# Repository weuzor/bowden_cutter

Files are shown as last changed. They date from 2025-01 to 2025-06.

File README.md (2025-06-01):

# Bowden Filament Cutter for the Voron Stealthburner

toolhead_CW2
toolhead_G2E
actuator

## Introduction
This toolhead integrated filament cutter cuts filament similar to the [filametrix mod](https://github.com/sorted01/Filametrix), on which it is based on, but uses a different approach for actuation by means of an external high torque servo which is connected to the toolhead via a bowden cable.
This way the cutting process is independent of toolhead position/movement and does not introduce any forces to the printer kinematics.

The modification consists of 4 components: a __modified extruder front body__ with bowden cable routing, a __modified printhead__ with shuttle guiding, the __blade shuttle__ and an __external actuator__ which can be clamped to the printer frame extrusions.

## Underlying designs

Because a filament cutter is only useful for multi material printing and multi material printing is very little fun without ECAS and filament sensors the following desings were used as a base instead of the original CW2 or [G2E](https://github.com/JaredC01/Galileo2) parts:

The modified extruder front body for the CW2 is based on [this design](https://www.printables.com/model/466692-stealthburner-cw2-filament-sensors-with-ecas-latch/files) with ECAS and two 5.5mm steelball/microswitch filament sensors

The modified extruder front body for the G2E is based on [this design](https://github.com/juliusjj25/G2E-Filametrix-Lever-Switch-Mod) with ECAS and two DF2-L3-D3 microswitch filament sensors

The printheads are based on the [original voron design printheads](https://vorondesign.com/voron_stealthburner) and the filametrix mod.

## Recent Changes

The original design worked fine, but when cutting harder filaments the required pulling force caused the blade shuttle to tilt when the spring was fully compressed.
Allthough still working this is not nice to look at and also results in unnecessary forces trying to push the extruder to the left and the printhead to the right.
To fix this a limit stop for the blade shuttle has been added to the extruder parts. This limit stop also acts as a switch which closes when the blade shuttle pulley bearing touches the limit stop.

Before:
https://github.com/user-attachments/assets/2ef3fe31-b55a-4e68-ab35-1ae4be9e5d9d

After:
https://github.com/user-attachments/assets/6c915074-667b-457e-bb91-5009137e85ce

After some time of use, the wire puller part of the actuator gets sliced in half by the thin wire.
Printing that part 100% infill helps, but to fix this issue for good the new part has two additional reinforcement screws. Also, some knurling has been added for more comfortable turning by hand.

---
# Modification Steps
## __Blade Shuttle__
### Required hardware
* 1 [ID 3 x OD 10 x 3 mm V-Groove Bearing](https://www.amazon.com/Atoplee-3x10x3mm-603VV-Groove-Bearings/dp/B0191I4UU2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)
* 1 M2.5 x 8 countersunk head screw  -OR-  M2.5 x 8 screw + Brass tube OD 3 mm / ID 2.5 mm, L 3 mm 
* 1 M2.5 washer
* 1 M2.5 x 5 x 3.5 heat set insert ([from this assortment](https://www.amazon.com/Threaded-Inserts-Assortment-Printing-Injection/dp/B0D49Y8J6M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))
* 1 compression spring 5.5 x 17 mm ([from this assortment](https://www.amazon.com/dp/B0DF21GRN1/ref=sr_1_1_sspa?__mk_de_DE=ÅMÅŽÕÑ&crid=2AKV6FXLFZY04&dib=eyJ2IjoiMSJ9.B9q0atkenJRq4xFEpuA6kf0xvpWVwtjE_6Jrg8n_wl6NHta9ITOqniu6mMLtZMFY2_GtR4F_p8Hx75KQDkPY7fpfaDna87tC5B3B3hsjJfN4gQ8lqOv1fjgLgXU953trXPpknKVWs0QRSiNBvWAiD5JjdxLaEr9TSl6Sqnwv4ecXGIxPsb15RojaRq2vxIcHnsdGiSbCrEg-Z74QEsWqzqf3JAr6EFOmu-LbFnp-Fyk.SwDMcXsodjg3r6qEAGHaBXy8vgAhajbzSszQWizHb5c&dib_tag=se&keywords=compression+spring&qid=1736647255&sprefix=compression+spring%2Caps%2C199&sr=8-1-spons&sp_csd=d2lkZ2V0TmFtZT1zcF9hdGY&psc=1))
* 1 [Hobby knife blade # 4](https://www.amazon.com/CIMAXIC-Manganese-Carving-Replacement-Supplies/dp/B0DJX43D77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) (cut or broken off at the end of the slot)
### Printed parts
| Picture | Description | STL | STEP |
| :---: | :---: | :---: | :---: |
| Shuttle | Blade shuttle  | [stl](https://github.com/weuzor/bowden_cutter/blob/main/STL/Blade%20Shuttle%20Parts/Shuttle.stl) | [step](https://github.com/weuzor/bowden_cutter/blob/main/CAD/Blade%20Shuttle%20Parts/Shuttle.step) |
### Assembly
* Break off the blade #4 near the end of the slot
* Install the heat set insert in the printed part 
* Assemble as shown.
  Note: Unfortunately the blade slot width is too small for a M3 screw to fit through, so M2.5 it has to be. However, the pulley inner diameter is 3 mm. In order to keep the pulley centered either use something like a brass tube OD 3 mm / ID 2.5 mm, L 3 mm or some heatshrink over the last 3 mm of the screw thread.
Altertnatively, a well tightened countersunk head screw can also be used.
Blade Shuttle Assembly Option 1
Blade Shuttle Assembly Option 2
blade_shuttle_and_spring

---
## Extruder 
### Required hardware
* PTFE Tube 1mm/2mm (inner tube) ([amazon](https://www.amazon.com/Quickun-Teflon-Tubing-Printer-Length/dp/B08Q83XNTT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))
* PTFE tube 2mm/4mm (outer tube) ([amazon](https://www.amazon.com/Quickun-Teflon-Tubing-Printer-Length/dp/B08Q813BQV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))
Note: The inner tube must fit into the outer tube. There are some tubes sold as 2mm inner diameter where this is possible and some where it is not.
If you cannot find appropriate outer tubing use one with 2.5 mm inner diameter instead.
* Nylon coated stranded steel wire 0.6 mm diameter ([amazon](https://www.amazon.com/BENECREAT-120-Feet-0-024inch-7-Strand-Stainless/dp/B07V3S947N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))
* 2 M1.6 x 3 Screws
* Appropriate wires and connectors for the toolhead board ([amazon](https://www.amazon.com/-/de/dp/B07S18D3RN/ref=sr_1_3?__mk_de_DE=ÅMÅŽÕÑ&crid=1RZAB60IVHYBH&dib=eyJ2IjoiMSJ9.JP_2nZAq6AIUN2Ys6pJIe-n5ac8OQy-y538Uq2oHmvDcXHvzcv4dG5FbggURIH8csrpxDbXchWkjJbL9Wnd__2dbPNm_JHhf7BwQRyl2se9LbzNYUa_mLgD2P_9uNHQ7wXC8hG95_oQttkY4tPxC2TDGVdnoDqUKz8O7TaGJxfN9JhqeRNCXgB3kL8-n2MlSkEJE6QzaYFYSTF0LyOS10SIeVXFIrw0yxfg5jZr6r8uPnggjhcjj2l3E-idA0MmEyoQc7XXNf0CMzDxTZ6QSrQz_a64CsHYt5yr4c1mwS6UVCC2pxMZv3POeD3AnGr-b_yHVYOl2kf7ldo9kumGNRLfi1l4th5g8wTo4Ldu6GA9U9YJdbALKhyqKVnMNHmcDDiQyaBrm9ThWswQUmxQod8EJ7Fdf6C8AlHTYVTGA11oSLuOa4UzsCe9qVAeEU7IB.hZfWDVEpQwBFOSOiRrlumKK7xhQUQ_z9sIYtyja4n0Q&dib_tag=se&keywords=mx+1.25&qid=1739485194&sprefix=mx+1.25%2Caps%2C197&sr=8-3) for SB2209)
### Printed parts
#### Galileo 2
| Picture | Description | STL | STEP |
| :---: | :---: | :---: | :---: |
| G2E_Front_Body | G2E Front Body with two ball less filament sensors, bowden tube routing, ECAS, cutter endstop | [stl](https://github.com/weuzor/bowden_cutter/blob/main/STL/Extruder%20Parts/G2E/G2E_Front_Body.stl) | [step](https://github.com/weuzor/bowden_cutter/blob/main/CAD/Extruder%20Parts/G2E/G2E_Front_Body.step) | 
#### Clockwork 2
| Picture | Description | STL | STEP |
| :---: | :---: | :---: | :---: |
| CW2 Front Body (new) | CW2 Front Body (new motor plate) with two filament sensors, bowden tube routing, ECAS, cutter endstop | [stl](https://github.com/weuzor/bowden_cutter/blob/main/STL/Extruder%20Parts/CW2/CW2_Front_Body_new_motorplate.stl) | [step](https://github.com/weuzor/bowden_cutter/blob/main/CAD/Extruder%20Parts/CW2/CW2_Front_Body_new_motorplate.step) |
| CW2 Front Body (old) | Same as above but compatible with the old motor plate | [stl](https://github.com/weuzor/bowden_cutter/blob/main/STL/Extruder%20Parts/CW2/CW2_Front_Body_old_motorplate.stl) | [step](https://github.com/weuzor/bowden_cutter/blob/main/CAD/Extruder%20Parts/CW2/CW2_Front_Body_old_motorplate.step) |
### Assembly
* Cut the 2mm/4mm PTFE tube to the required length for the installation (depending on printer size and where the actuator will be located).
* Cut the 1mm/2mm PTFE tube approximately 10 cm longer than the 2mm/4mm tube
* Tie a [figure-8-knot](https://www.animatedknots.com/figure-8-knot) in the 0.6 mm wire and cut it approximately 10 cm longer than the 1mm/2mm PTFE tube (measured from the knot)
* Check that the OD 4 mm PTFE fits into its recess on top of the printed body. Clear out by hand with a 4mm drill if necessary.
* Check that the 0.6 mm wire can be inserted in the small holes at the bottom aof the printed body. Clear out by hand with a 1 mm drill if necessary.
* Push the OD 2 mm PTFE from the top into the printed body until it is fully inserted. Might need a bit of persuasion here and there but is definitely doable. A drop of oil and a 2 steps forward one step back movement strategy helps. If you can insert the 0.6 mm wire from the opposite side without catching the on the PTFE tube edge you are there.
* Slide the ID 2mm OD 4mm PTFE over the ID 1 mm OD 2mm PTFE tube and push firmly into its recess in the printed part.
* Cut the inner PTFE tube flush with the outer tube
* Push the 0.6 mm wire through the long hole at the bottom of the printed part and pull firmly to fully tighten the knot. Clip off the excess wire leaving about 1 mm.
* After a U-turn push the wire through the PTFE until it comes out the other end
* Route the cables along the cable path as shown and insert approx. 2mm of tinned wire into each hole in the limit stop and press downward.
* Screw in the two M1.6 screws into the two holes (above the wires) in the limit stop as shown. Check for continuity with a Multimeter (screw head to end of wire).
* Complete the extruder with the modified body part
bowden_installation_cw2
bowden_installation_g2e
cut_sensor_inst
cut_sensor

---
## Printhead
### Required hardware
* 1 M3 Nut
* Filament path PTFE Tube
### Printed parts
#### E-RV
| Picture | Description | STL | STEP |
| :---: | :---: | :---: | :---: |
| E-RV (no ADXL)_Front E-RV (no ADXL)_Back | E-RV Printhead (symmetric, no ADXL mount) with blade shuttle guiding | [front](https://github.com/weuzor/bowden_cutter/blob/main/STL/Printhead%20Parts/E-RV/E-RV%20(no%20ADXL)_Front.stl) [back](https://github.com/weuzor/bowden_cutter/blob/main/STL/Printhead%20Parts/E-RV/E-RV%20(no%20ADXL)_Back.stl) | [front](https://github.com/weuzor/bowden_cutter/blob/main/CAD/Printhead%20Parts/E-RV/E-RV%20(no%20ADXL)_Front.step) [back](https://github.com/weuzor/bowden_cutter/blob/main/CAD/Printhead%20Parts/E-RV/E-RV%20(no%20ADXL)_Back.step) |
| E-RV_Front E-RV_Back | Stock E-RV printhead with blade shuttle linear guiding  | [front](https://github.com/weuzor/bowden_cutter/blob/main/STL/Printhead%20Parts/E-RV/E-RV_Front.stl) [back](https://github.com/weuzor/bowden_cutter/blob/main/STL/Printhead%20Parts/E-RV/E-RV_Back.stl) | [front](https://github.com/weuzor/bowden_cutter/blob/main/CAD/Printhead%20Parts/E-RV/E-RV_Front.step) [back](https://github.com/weuzor/bowden_cutter/blob/main/CAD/Printhead%20Parts/E-RV/E-RV_Back.step) |
#### P-RPDV2
| Picture | Description | STL | STEP |
| :---: | :---: | :---: | :---: |
| P-RPDV2_Front P-RPDV2_Back | Stock P-RPDV2 printhead with blade shuttle linear guiding  | [front](https://github.com/weuzor/bowden_cutter/blob/main/STL/Printhead%20Parts/P-RPDV2/P-RPDV2_Front.stl) [back](https://github.com/weuzor/bowden_cutter/blob/main/STL/Printhead%20Parts/P-RPDV2/P-RPDV2_Back.stl) | [front](https://github.com/weuzor/bowden_cutter/blob/main/CAD/Printhead%20Parts/P-RPDV2/P-RPDV2_Front.step) [back](https://github.com/weuzor/bowden_cutter/blob/main/CAD/Printhead%20Parts/P-RPDV2/P-RPDV2_Back.step) |
#### P-DRG
| Picture | Description | STL | STEP |
| :---: | :---: | :---: | :---: |
| P-DRG_Front P-DRG_Back | Stock P-DRG printhead with blade shuttle linear guiding  | [front](https://github.com/weuzor/bowden_cutter/blob/main/STL/Printhead%20Parts/P-DRG/P-DRG_Front.stl) [back](https://github.com/weuzor/bowden_cutter/blob/main/STL/Printhead%20Parts/P-DRG/P-DRG_Back.stl) | [front](https://github.com/weuzor/bowden_cutter/blob/main/CAD/Printhead%20Parts/P-DRG/P-DRG_Front.step) [back](https://github.com/weuzor/bowden_cutter/blob/main/CAD/Printhead%20Parts/P-DRG/P-DRG_Back.step) |
### Assembly

*  Assemble as usual. Don't forget the ptfe tube before inserting the M3 nut
*  Check that the spring followed by the blade shuttle can be inserted into the guide and moves smoothly
*  Optionally lubricate the contact surfaces with a tiny amount of petroleum jelly
*  Remove blade shuttle and spring for now

shuttle_insert
shuttle_inserted
shuttle_cut_pos

---

## Actuator

### Required hardware
* 1 [Miuzei 25kg Servo](https://www.amazon.com/Miuzei-Waterproof-Compatible-Steering-Horn（270°）/dp/B0C5LTKBD4/ref=sr_1_8?crid=1RKYBOP2MC3X5&dib=eyJ2IjoiMSJ9.5BsLf39L1mf4c0ZP7ihNfBcTucSXzqrylZ5wPm1FCZv5wywgXEZg8dzhwaeOFhQKoNJWUU3jyFHMdI_3LbyACR33Kmu10v0dFclbm8f5Wi29QDhH9nP2OV--_QzTVKYJtExh0ru4tfxeGZCQR1O45u62ZbZ7vDu3kLlgaTb16AaTpBTvtNuceMTKtBs_AoUUucpRz8daa88bTl0jgQc3zPhm-HagKRoHf3OntGky96HSfhzFnBvgk_47v8lISK_yfMscdNapOXOrRZh-QcGOnMjBkn3Q2Z7BgruQQfZQg2Dosnl2Lo9nXBHNfwN3vcMU5GP0gaHs4a_NLZ4IQaibOTazYqvwFS1RVYBUXIoopTEp9_zGB0G0D4ItZ_uS9RlO99e3KistSzl-Ztef1v2GcOVwoBLVwRXQxPFw_HdreqIyc5iuHV7sSS0DYl1A8Qrn._j4nZ8dHQSZ3S-M3PkTiq-Yw1uM0tN85bQJuZTc3dog&dib_tag=se&keywords=miuzei&qid=1738536290&sprefix=miuzei%2Caps%2C181&sr=8-8&th=1) (or similar) + supplied screws + round servo horn
* 4 M3 x 4 x 5 heat set inserts
* 4 M3 washer
* 2 M3 x 5 screws
* 2 M3 x 12 screws
* 4 M2 x 8 Tapping screws
* 1 ECAS Collet (rubber part removed)
### Printed parts
| Picture | Description | STL | STEP |
| :---: | :---: | :---: | :---: |
| Servo_Frame_Mount | Actuator servo to frame mount | [stl](https://github.com/weuzor/bowden_cutter/blob/main/STL/Actuator%20Parts/Servo_Frame_Mount.stl) | [step](https://github.com/weuzor/bowden_cutter/blob/main/CAD/Actuator%20Parts/Servo_Frame_Mount.step) |
| Servo_Frame_Mount_Mirrored | Actuator servo to frame mount, mirrored | [stl](https://github.com/weuzor/bowden_cutter/blob/main/STL/Actuator%20Parts/Servo_Frame_Mount_mirrored.stl) | [step](https://github.com/weuzor/bowden_cutter/blob/main/CAD/Actuator%20Parts/Servo_Frame_Mount_mirrored.step) |
| Servo_Frame_Mount_Clamp_Insert | clamp insert ( x2 ) | [stl](https://github.com/weuzor/bowden_cutter/blob/main/STL/Actuator%20Parts/Servo_Frame_Mount_Clamp_Insert_x2.stl) | [step](https://github.com/weuzor/bowden_cutter/blob/main/CAD/Actuator%20Parts/Servo_Frame_Mount_Clamp_Insert_x2.step) |
| Wire_Puller | wire puller servo attachment| [stl](https://github.com/weuzor/bowden_cutter/blob/main/STL/Actuator%20Parts/Wire_Puller.stl) | [step](https://github.com/weuzor/bowden_cutter/blob/main/CAD/Actuator%20Parts/Wire_Puller.step) |
| Wire_Puller_V2 | wire puller servo attachment with reinforcement screws | [stl](https://github.com/weuzor/bowden_cutter/blob/main/STL/Actuator%20Parts/Wire_Puller_strong.stl) | [step](https://github.com/weuzor/bowden_cutter/blob/main/CAD/Actuator%20Parts/Wire_Puller_strong.step) |
### Assembly
* Press the ECAS collet and two clamp inserts into the servo mount body as shown
* Install the two heat set inserts in the wire puller part and assemble as shown with the round servo horn which comes with the servo.
* Combine everything as shown
actuator_body
actuator_puller
actuator_servoy

## FINAL STEPS
actuator_wire
shuttle_pos

* Assemble the toolhead with the modified extruder and printhead
* Run the bowden wire through the actuator hole and insert the ptfe tubes into the ecas collet
* Insert the blade shuttle and place the wire loop around the pulley
* Loosen the wire clamp bolts and route the wire on the actuator servo as shown
* Adjust the wire length so that the blade shuttle is flush with the printhead edge and the servo is approximately in the shown position (servo angle 90 deg)
* Tighten the wire clamp bolts

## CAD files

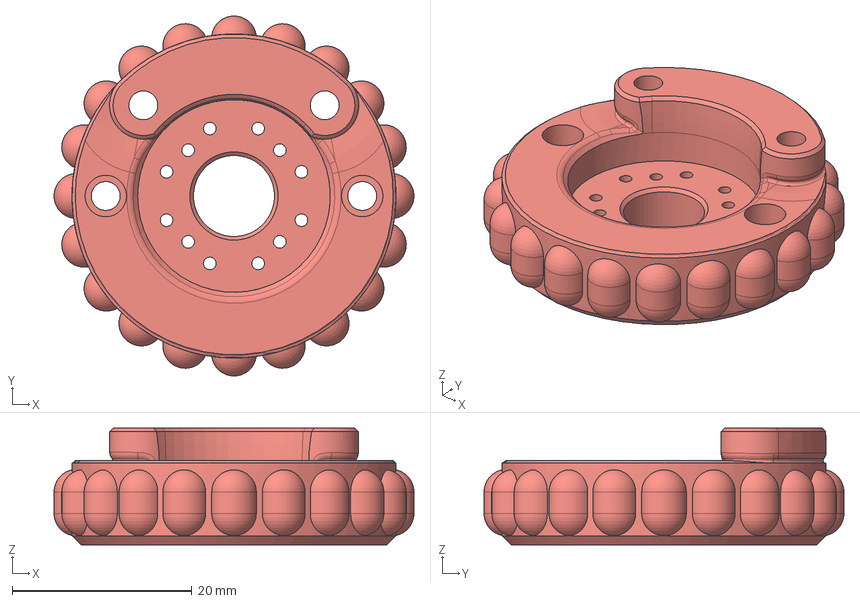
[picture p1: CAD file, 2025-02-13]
CAD/Actuator Parts/Wire_Puller_strong.step
40.0 x 40.0 x 13.0 mm

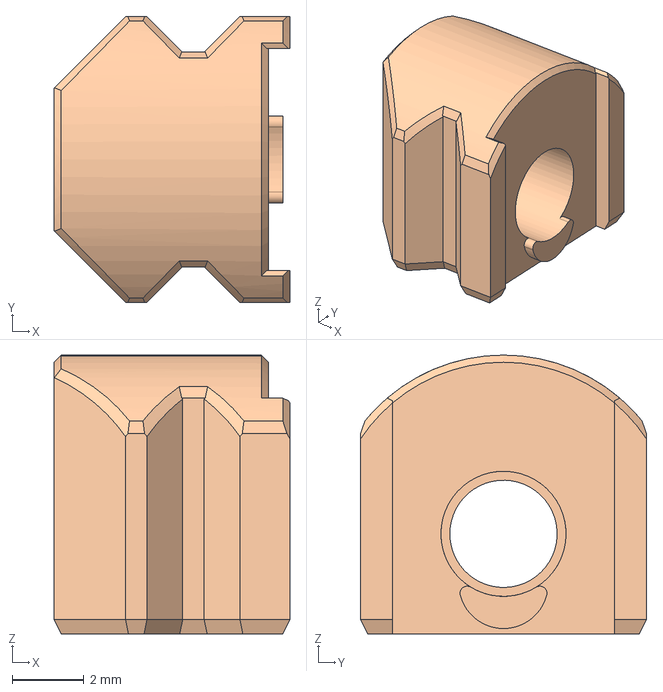
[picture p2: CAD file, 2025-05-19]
CAD/Blade Shuttle Parts/Shuttle v2.step
6.60 x 8.00 x 7.80 mm

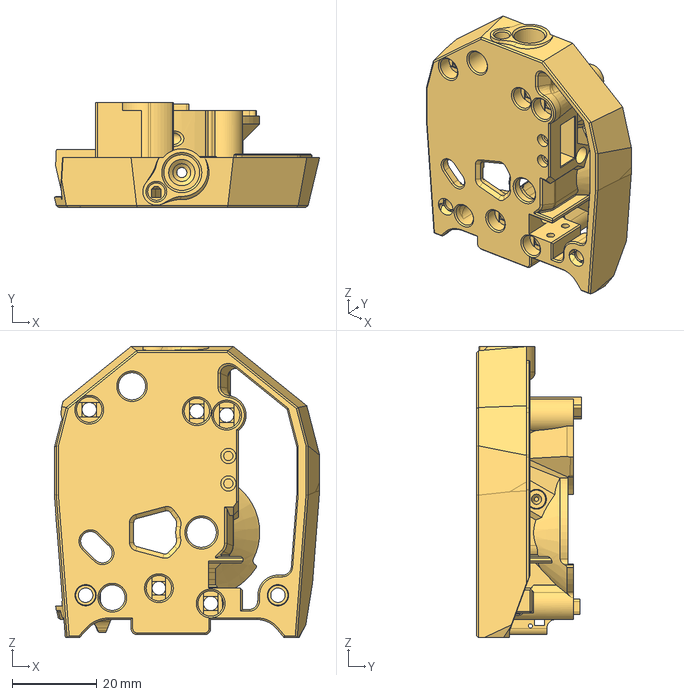
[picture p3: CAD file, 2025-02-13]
CAD/Extruder Parts/CW2/CW2_Front_Body_new_motorplate.step
62.6 x 24.7 x 68.7 mm

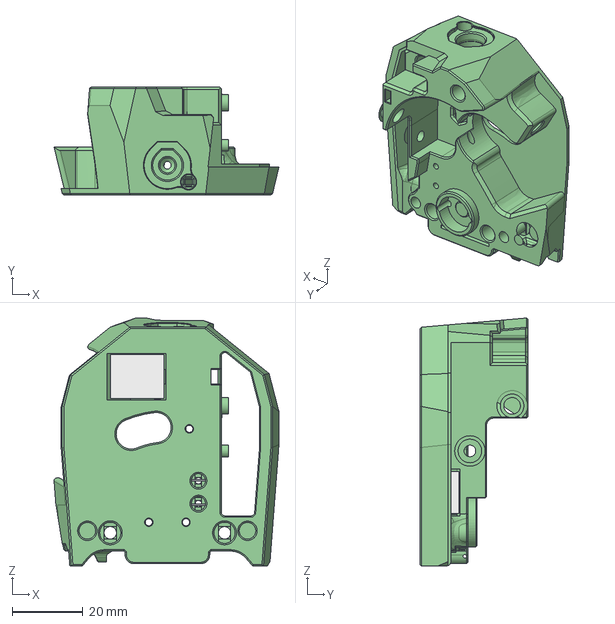
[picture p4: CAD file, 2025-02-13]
CAD/Extruder Parts/G2E/G2E_Front_Body.step
63.8 x 30.6 x 70.3 mm

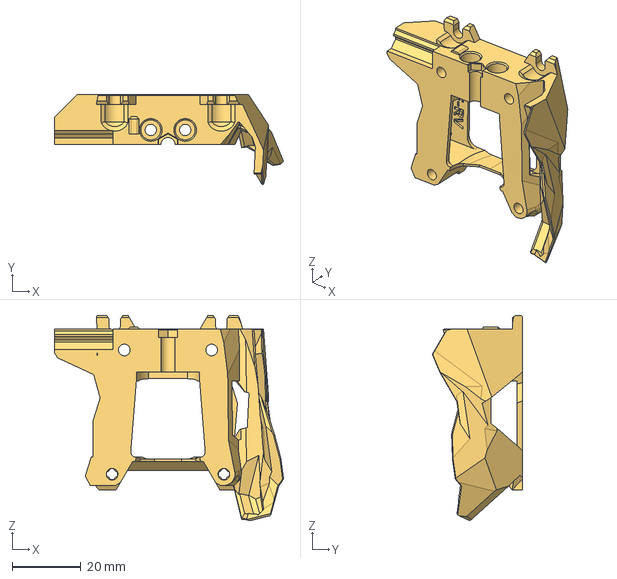
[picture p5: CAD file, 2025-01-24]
CAD/Printhead Parts/E-RV/E-RV_Back.step
66.6 x 26.3 x 59.7 mm

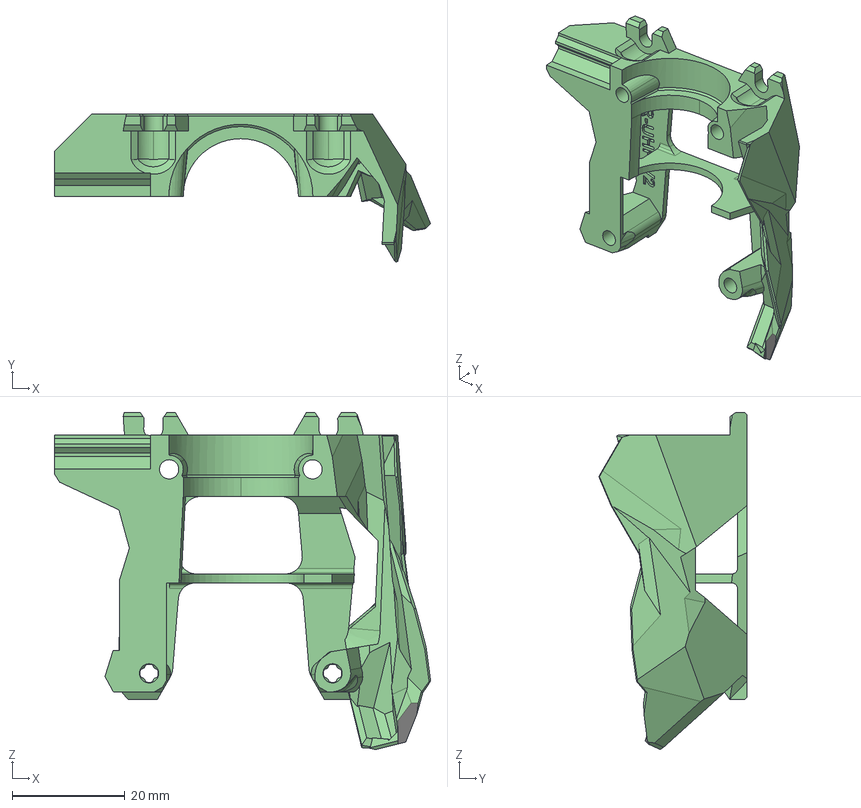
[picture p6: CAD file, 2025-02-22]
CAD/Printhead Parts/P-RPDV2-UHF/P-RPDV2-UHF_Rear.step
66.6 x 26.3 x 59.7 mm

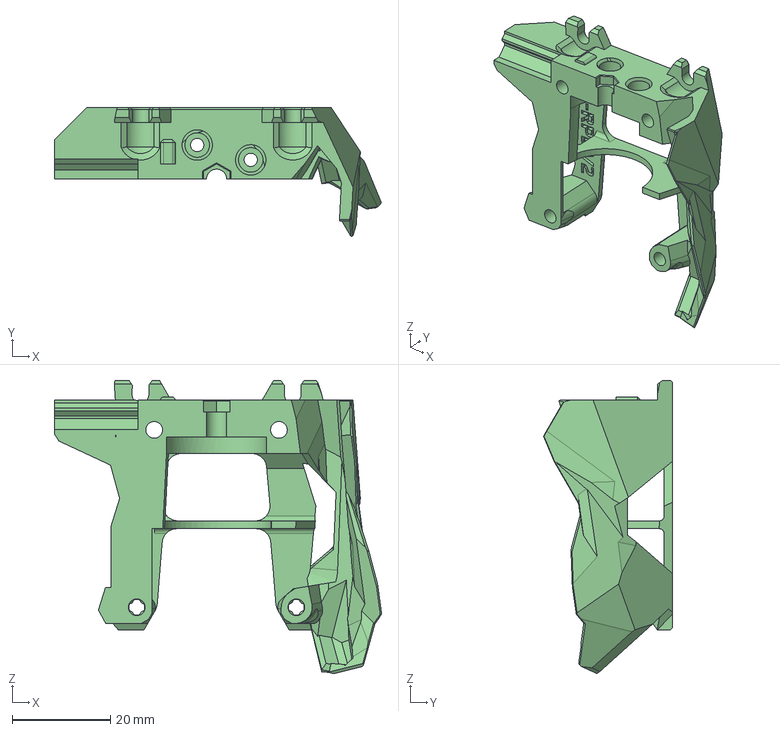
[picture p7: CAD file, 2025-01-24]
CAD/Printhead Parts/P-RPDV2/P-RPDV2_Back.step
66.6 x 26.3 x 59.7 mm

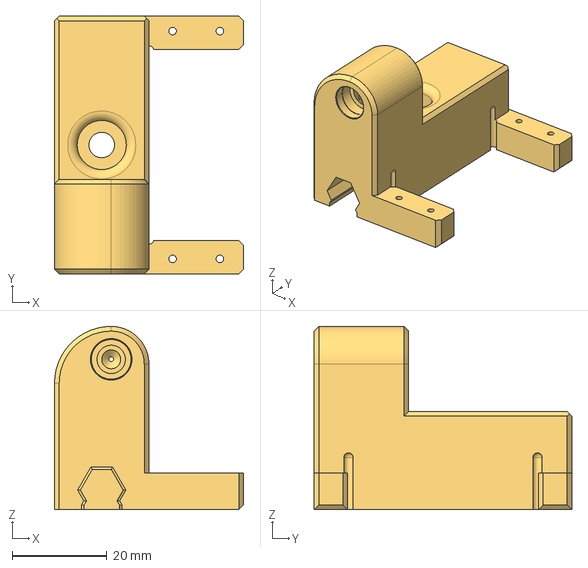
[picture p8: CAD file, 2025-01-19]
CAD/Actuator Parts/Servo_Frame_Mount_mirrored.step
40.0 x 54.5 x 38.8 mm

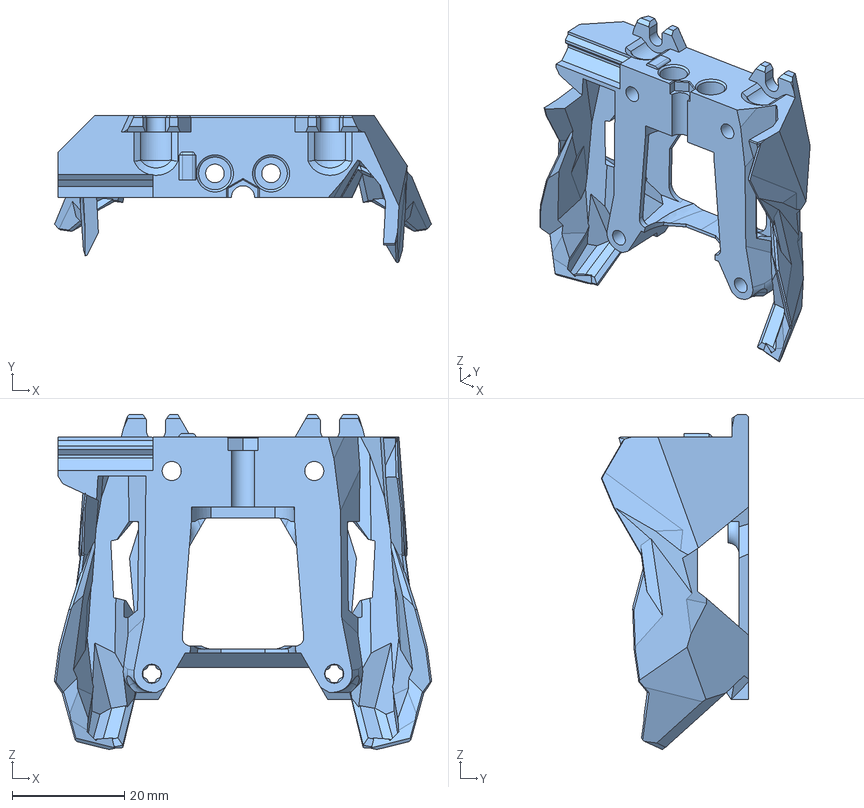
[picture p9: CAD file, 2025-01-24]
CAD/Printhead Parts/E-RV/E-RV (no ADXL)_Back.step
67.2 x 26.3 x 59.7 mm

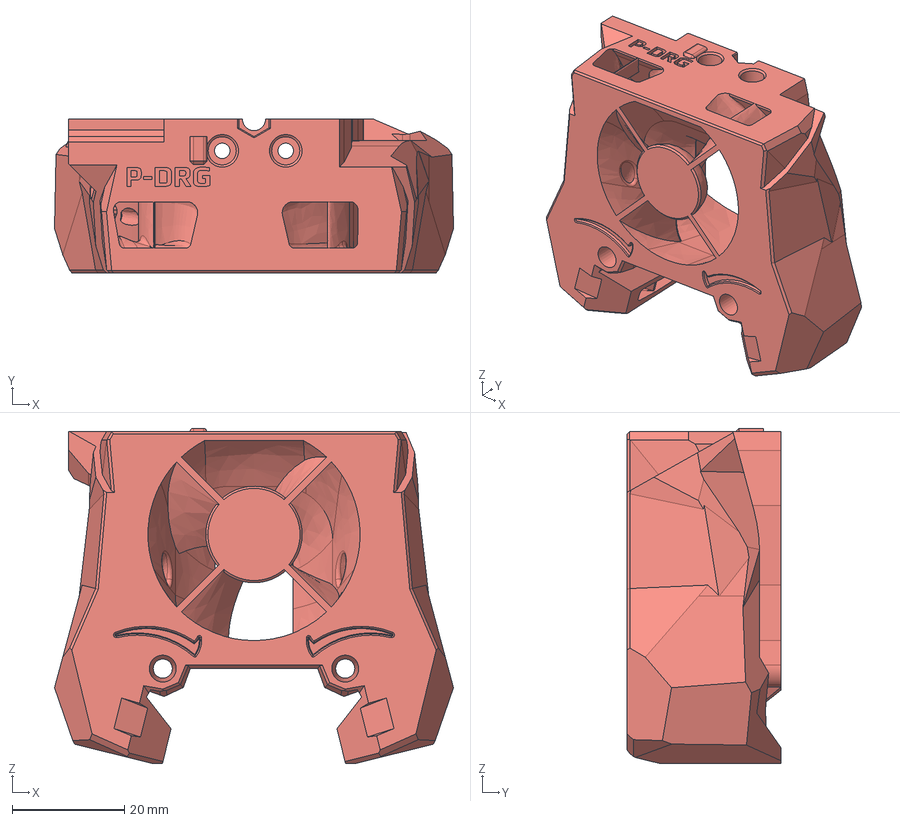
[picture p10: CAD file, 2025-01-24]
CAD/Printhead Parts/P-DRG/P-DRG_Front.step
71.1 x 27.4 x 59.7 mm

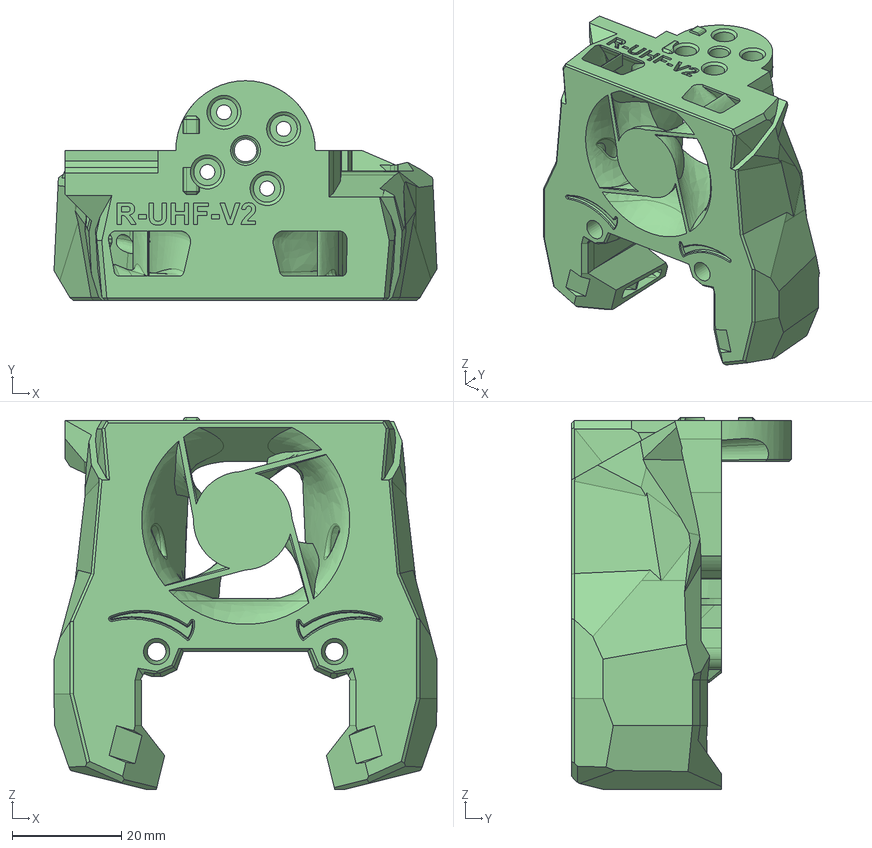
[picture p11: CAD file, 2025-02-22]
CAD/Printhead Parts/P-RPDV2-UHF/P-RPDV2-UHF_Front.step
70.0 x 40.2 x 68.0 mm

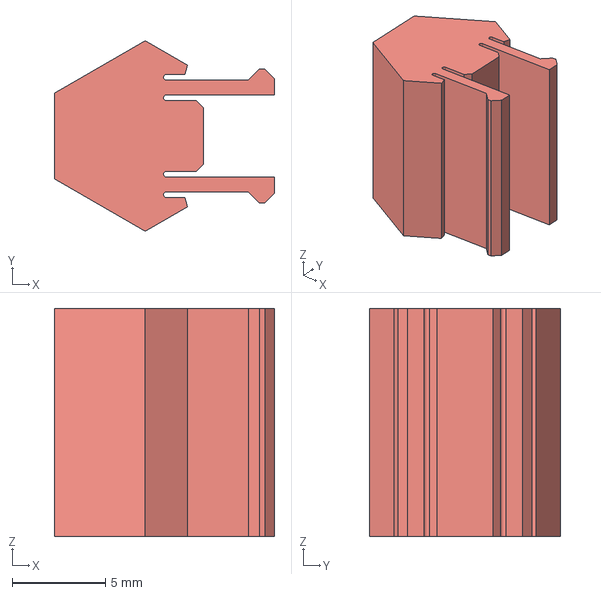
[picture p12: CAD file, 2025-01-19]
CAD/Actuator Parts/Servo_Frame_Mount_Clamp_Insert_x2.step
11.8 x 10.2 x 12.2 mm

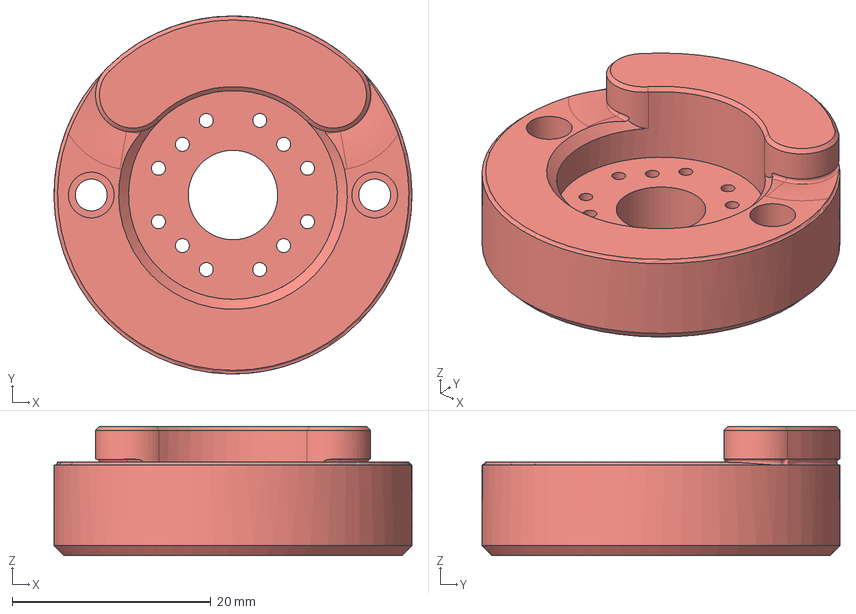
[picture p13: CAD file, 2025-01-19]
CAD/Actuator Parts/Wire_Puller.step
36.0 x 36.0 x 13.0 mm

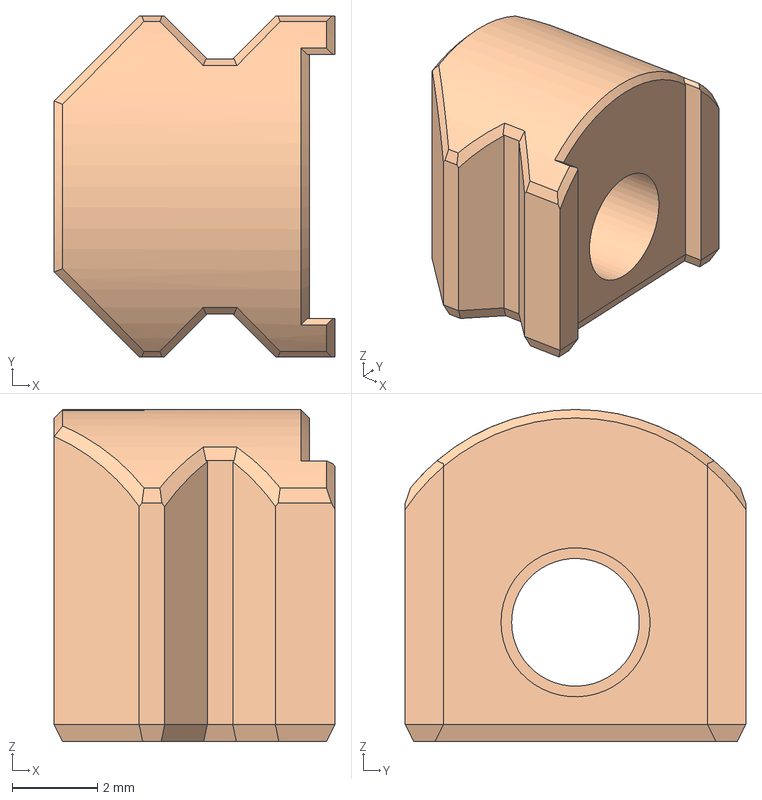
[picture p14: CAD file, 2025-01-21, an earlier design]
CAD/Blade Shuttle Parts/Shuttle.step
6.60 x 8.00 x 7.80 mm

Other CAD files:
CAD/Printhead Parts/P-DRG/P-DRG_Back.step
CAD/Actuator Parts/Servo_Frame_Mount.step
CAD/Extruder Parts/CW2/CW2_Front_Body_old_motorplate.step
STL/Actuator Parts/Servo_Frame_Mount.stl
STL/Actuator Parts/Servo_Frame_Mount_Clamp_Insert_x2.stl
STL/Actuator Parts/Servo_Frame_Mount_mirrored.stl
STL/Actuator Parts/Wire_Puller.stl
STL/Actuator Parts/Wire_Puller_strong.stl
STL/Blade Shuttle Parts/Shuttle.stl
STL/Extruder Parts/CW2/CW2_Front_Body_new_motorplate.stl
STL/Extruder Parts/CW2/CW2_Front_Body_old_motorplate.stl
STL/Extruder Parts/G2E/G2E_Front_Body.stl
STL/Printhead Parts/E-RV/E-RV (no ADXL)_Back.stl
STL/Printhead Parts/E-RV/E-RV_Back.stl
STL/Printhead Parts/P-DRG/P-DRG_Back.stl
STL/Printhead Parts/P-DRG/P-DRG_Front.stl
STL/Printhead Parts/P-RPDV2/P-RPDV2_Back.stl

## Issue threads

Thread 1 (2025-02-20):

P-RPDV2-UHF

wgkbfcp, 2025-02-20:
Hello, I really like your setup and would love to experience it, but my print head doesn't match. Can I adapt it to this P-RPDV2-UHF print head? Thank you.

weuzor, 2025-02-20:
Where can I find this P-RPDV2-UHF printhead?

feirouu, 2025-02-22:
#2

wgkbfcp, 2025-02-22:
> 我在哪里可以找到这个 P-RPDV2-UHF 打印头？

https://github.com/IRTrail/G2E-Filametrix/tree/main/Printheads/Rapido%202%20UHF/STL
Hello, this link has this print head model

weuzor, 2025-02-22:
would need step files

weuzor, 2025-02-22:
I have placed the P-RPDV2-UHF Printhead here:
https://github.com/weuzor/bowden_cutter/blob/main/CAD/Printhead%20Parts/P-RPDV2-UHF/P-RPDV2-UHF.step

wgkbfcp, 2025-02-23:
> I have placed the P-RPDV2-UHF Printhead here: https://github.com/weuzor/bowden_cutter/blob/main/CAD/Printhead%20Parts/P-RPDV2-UHF/P-RPDV2-UHF.step
>
> Please let me know if it is what you wanted.

Sorry, this is in Steam format. thank

https://github.com/IRTrail/G2E-Filametrix/tree/main/Printheads/Rapido%202%20UHF/CAD

Closed 2025-02-22.

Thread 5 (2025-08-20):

How did you add an endstop to the servo?

feirouu, 2025-08-20:
Hey, I saw you added an endstop switch for the servo in your project. Since Klipper doesn't have this feature by default, I was wondering how you implemented it? Could you share some details on how you got it working?
Thanks!

weuzor, 2025-08-31:
hi!
for hardware setup I use
`
[servo bowden_cutter_actuator]
pin: PG12         
maximum_servo_angle:   180
minimum_pulse_width:   0.0005
maximum_pulse_width:   0.0025
initial_angle:         90       #  servo release angle. ( ~ max angle / 2 , cutter blade clear of filament path)

[gcode_button BOWDEN_CUTTER_ENDSTOP]
pin: ^!sb2209: PB9
press_gcode:
release_gcode:
`

and for the actuation this macro
`[gcode_macro _BOWDEN_CUTTER_ACTION]
#
variable_reverse_servo:  False  # True for actuator build with mirrored body
#
# Only relevant when no cutter endstop is installed (fixed cutting time):
variable_pull_time:       1000  ;time the servo needs to cut the hardest to cut filament reliably [ms]
#
# Only relevant when a shuttle endstop switch is installed and configured (variable cutting time):
variable_evac_time:        280  ;time the blade shuttle needs to travel from endstop to released position [ms]
variable_loops:             10  ;maximum number of unsuccessful endstop probing attempts before failing cut
#
gcode:
    SAVE_GCODE_STATE NAME=_BOWDEN_CUTTER_ACTION_STATE
    {% set blade_endstop_switch_installed = "gcode_button bowden_cutter_endstop" in printer.configfile.settings %}
    {% set pull_angle = 0 if reverse_servo|lower == 'true' else printer.configfile.settings['servo bowden_cutter_actuator'].maximum_servo_angle|int %}
    {% set release_angle = printer.configfile.settings['servo bowden_cutter_actuator'].initial_angle|int %}
    {% set rip_length = params.RIP_LENGTH|default(0.4)|float %}
    {% set rip_speed = params.RIP_SPEED|default(5)|float %}
    M400
    {% if "gcode_button bowden_cutter_endstop" in printer.configfile.settings and params.FORCE_FIXED|default('false')|lower == 'false' %}
        ## cut with variable cutting time (endstop switch installed)
        _BOWDEN_CUTTER_CUT N={loops} PULL_ANGLE={pull_angle}
        _BOWDEN_CUTTER_CHECK_CUT
        _BOWDEN_CUTTER_RELEASE N={loops} EVAC_TIME={evac_time}
        _BOWDEN_CUTTER_CHECK_RELEASE
    {% else %}
        ## cut with fixed cutting time (no endstop switch installed)
        RESPOND MSG="Cutting filament .."
        SET_SERVO SERVO=bowden_cutter_actuator ANGLE={pull_angle}
        G4 P{pull_time}
        M83
        G1 E-{rip_length} F{rip_speed * 60}
        SET_SERVO SERVO=bowden_cutter_actuator ANGLE={release_angle}
        G4 P{pull_time}
        G1 E{rip_length} F{rip_speed * 60}
        M400
        RESPOND MSG=".. finished cutting filament"
    {% endif %}
    RESTORE_GCODE_STATE NAME=_BOWDEN_CUTTER_ACTION_STATE

[gcode_macro _BOWDEN_CUTTER_CUT]
gcode:
    {% set pull_angle = params.PULL_ANGLE|default(0)|int %}
    {% set loops = params.N|default(0)|int %}
    RESPOND MSG="Cutting filament .."
    SET_SERVO SERVO=bowden_cutter_actuator ANGLE={pull_angle}
    {% for i in range(loops) %}
        _BOWDEN_CUTTER_CUT_DELAY
    {% endfor %}

[gcode_macro _BOWDEN_CUTTER_CUT_DELAY]
gcode:
    {% if printer['gcode_button BOWDEN_CUTTER_ENDSTOP'].state != 'PRESSED' %}
        G4 P1
        M400
    {% endif %}

[gcode_macro _BOWDEN_CUTTER_CHECK_CUT]
gcode:
    {% if printer['gcode_button BOWDEN_CUTTER_ENDSTOP'].state == 'PRESSED' %}
        RESPOND MSG=".. filament successfully cut"
    {% else %}
        RESPOND TYPE=error MSG=".. failed to cut filament"
        _BOWDEN_CUTTER_EXCEPTION
    {% endif %}

[gcode_macro _BOWDEN_CUTTER_RELEASE]
gcode:
    {% set release_angle = printer.configfile.settings['servo bowden_cutter_actuator'].initial_angle|int %}
    {% set loops = params.N|default(0)|int %}
    {% set blade_evac_time = params.BLADE_EVAC_TIME|default(150)|int %}
    {% set rip_length = params.RIP_LENGTH|default(0.4)|float %}
    {% set rip_speed = params.RIP_SPEED|default(5)|float %}
    RESPOND MSG="Releasing blade .."
    M83
    G1 E-{rip_length} F{rip_speed * 60}
    SET_SERVO SERVO=bowden_cutter_actuator ANGLE={release_angle}
    {% for i in range(loops) %}
        _BOWDEN_CUTTER_RELEASE_DELAY
    {% endfor %}
    G4 P{blade_evac_time}
    G1 E{rip_length} F{rip_speed * 60}
    M400

[gcode_macro _BOWDEN_CUTTER_RELEASE_DELAY]
gcode:
    {% if printer['gcode_button BOWDEN_CUTTER_ENDSTOP'].state == 'PRESSED' %}
        G4 P1
        M400
    {% endif %}

[gcode_macro _BOWDEN_CUTTER_CHECK_RELEASE]
gcode:
    {% if printer['gcode_button BOWDEN_CUTTER_ENDSTOP'].state != 'PRESSED' %}
        RESPOND MSG=".. blade successfully released"
    {% else %}
        RESPOND TYPE=error MSG=".. failed to release blade"
        _BOWDEN_CUTTER_EXCEPTION
    {% endif %}

[gcode_macro _BOWDEN_CUTTER_EXCEPTION]
gcode:
    SET_SERVO SERVO=bowden_cutter_actuator ANGLE={printer.configfile.settings['servo bowden_cutter_actuator'].initial_angle|int }
    {% if printer.mmu.print_state == 'printing' %}
        MMU_PAUSE MSG="Check bowden cutter before resuming print"
    {% endif %}`

Closed 2025-08-31.
